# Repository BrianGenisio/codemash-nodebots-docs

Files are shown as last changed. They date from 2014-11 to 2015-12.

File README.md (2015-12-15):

# Website for [NodeBots.CodeMash.org](http://nodebots.codemash.org)

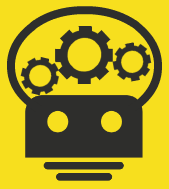
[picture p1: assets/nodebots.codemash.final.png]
NodeBots CodeMash logo


This site uses [Jekyll](http://jekyllrb.com/) and GitHub Pages to host.  **Pull Requests are accepted!**  If it is just a small Markdown change, you can go into the "_posts" folder right from GitHub to edit and create an automatic fork/PR without cloning the repo onto your machine.  If you want to do more, install Jekyll, clone the repo, and run `jekyll serve --watch` from the "gh-pages" branch.

**Note**: This is the site for Nodebots @Codemash 2015.  For the 2016 event, please see [the NodeBots Unleashed site.](https://github.com/CareEvolution/nodebots-unleashed-codemash-docs)

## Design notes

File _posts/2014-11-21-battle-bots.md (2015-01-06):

---
layout: page
title: "Battle Bots"
category: act
date: 2014-11-21
order: 0
---

One of the activities at this event is "Battle Bots".  When you build a battle bot, you are competing in a head-to-head battle, much like a wrestling or sumo match.  There will be a ring, and your job will be to push your opponent out of the ring.

**Here are the rules**

0. Build your bot however you want, but use the two continuous servos as your primary drive mechanism.
0. The arena is a hexagon, 1 meter wide, on carpet.
0. You have one minute to knock your opponent completely out of the arena.  This is considered a KO.
0. If after one minute, a KO is not achieved, the bot with their Arduino closest to the center dot wins.
0. We will set this up as a randomized single-elimination bracket, so build your bot to fight more than once.
0. All rules are subject to interpetation by the referee.

You have full access to the maker space.  If you build the reference kit, you are very unlikely to win.  You need to innovate.  What kinds of modifications can you make to give yourself an advantage?

**Here are some examples of NodeBots battling it out**

<iframe width="640" height="360" src="//www.youtube.com/embed/pmp_hCg6jGQ" frameborder="0" allowfullscreen></iframe>

**And here is an example of an intense battle**

<iframe width="640" height="360" src="//www.youtube.com/embed/OA97THHGgEo" frameborder="0" allowfullscreen></iframe>

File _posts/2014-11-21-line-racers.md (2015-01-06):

---
layout: page
title: "Line Racers"
category: act
date: 2014-11-21
order: 1
---

If you are feeling more like a pacifist and you don't want to fight your bot, then perhaps you would like to race your bot?  Your line racer will follow a dark line on a white background and will traverse the path as quickly as possible.  You will be given a "reflectance sensor kit" which can be used to detect your position on the line.  

**Here are the rules:**

0. You may use any materials you wish to build your bot.
0. You will be timed as you traverse the track once without user intervention.
0. A 6" perpendicular line will indicate the start/finish line (same spot).  Your sensor will start on this line and your bot must stop on the line.  Failure to stop will result in a 6 second penalty.
0. Your line sensor must stay on the line at all times.  Failure to do so will result in a 2 second penalty for each divergence. The referee reserves the right to disqualify any both which flagrantly diverges from the course.
0. The minimum turn radius will be 2 inches.
0. There is at least 3 inches between the edge of the line and the edge of the platform or other line.
0. Bots which take more than 1 minute to complete will be disqualified.
0. All rules are subject to interpetation by the referee.

**Here is an example of a line-following bot**

<iframe width="640" height="360" src="//www.youtube.com/embed/i6n4CwqQer0" frameborder="0" allowfullscreen></iframe>

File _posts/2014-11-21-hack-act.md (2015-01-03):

---
layout: page
title: "Hacking"
class: hack-act
category: act
date: 2014-11-21
order: 2
---

Perhaps you don't want to compete with anyone.  That is totally fine!  You can just hack.  Come up with an idea, and go to town.  We have a fully-stocked lab with all sorts of chassis, building materials, controller boards, electronic components, and tools.  Checkout our inventory for more information about what we have for you to build with.  Build whatever you want.  Just make sure to "show and tell" at the end.  We can't wait to see what you build.

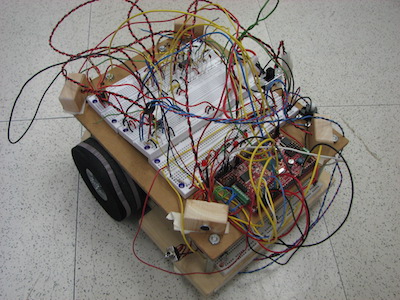
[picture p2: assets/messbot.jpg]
messy bot


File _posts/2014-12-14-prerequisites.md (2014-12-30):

---
layout: page
title: "Prerequisites"
category: tut
date: 2014-12-23
order: 0
---

0. [Node.js (required)](#nodejs)
0. [Arduino IDE (required for Windows)](#arduino)
0. [Git (optional but recommended)](#git)
0. [Visual Studio Tools (optional)](#vs)
0. [Sublime Text (optional)](#sublime)

> All of the files have been packaged up into a [single location](https://www.dropbox.com/sh/v4krjmg3rcctdvw/AADja4svpkxiA2zTXFDZe0PYa?dl=0) for your convenience.

## Node.js (required) 
This is the only required software.  These are [NodeBots](http://nodebots.io) so they require [Node.js](http://nodejs.org) to run. Node is a JavaScript runtime based on the V8 engine.  It is how you will be running the code today.  Just download and install it.

- [OSX](http://nodejs.org/dist/v0.10.35/node-v0.10.35.pkg)
- [Windows 32bit](http://nodejs.org/dist/v0.10.35/node-v0.10.35-x86.msi)
- [Windows 64bit](http://nodejs.org/dist/v0.10.35/x64/node-v0.10.35-x64.msi)

## Arduino IDE (required for Windows)
The Arduino IDE is useful if you want to run native C code with your Arduino boards.  In this lab, we will be using JavaScript on a host computer which communicates over serial to the Arduino.  We've pre-loaded the required code on your board, so you don't need the Arduino IDE for much.  It does, however, install some necessary drivers for USB to Serial in Windows.  You might want it, also, if you want to do more advanced things with your hardware.  After you install it, run it once.

- [OSX](http://arduino.cc/download.php?f=/arduino-1.0.6-macosx.zip)
- [Windows](http://arduino.cc/download.php?f=/arduino-1.0.6-windows.exe)

## Git (recommended)
The open source community runs on [Git](http://git-scm.com/) and [GitHub](http://github.com).  All of our examples as well as anything else you are likely to want to bring in will be on Git.  Because of this, we recommend that you have Git.  You can get away with not installing it if you prefer -- you can just download Zip files from GitHub -- so it is optional.  If you don't already have Git installed, we recommend installing the GitHub client on Windows.  For the Mac, open up a command line and type `git --version`.  If it is already installed, you will get a version back.  If not, OSX will ask you to install the necessary components automatically.

- [Windows](https://github-windows.s3.amazonaws.com/GitHubSetup.exe)

## Visual Studio Tools for Node.js (optional for Windows)
Some Windows users prefer the Visual Studio environment when developing in Node.  If you think you'd like to do that, you can install the tools for Visual Studio 2012 or 2013

- [VS 2012](http://nodejstools.codeplex.com/downloads/get/946896)
- [VS 2013](http://nodejstools.codeplex.com/downloads/get/946895)

## Sublime Text (optional)
You need a text editor.  Chances are that you already have one that you like.  If not, try Sublime Text.  It is pretty nice.

- [OSX](http://c758482.r82.cf2.rackcdn.com/Sublime%20Text%202.0.2.dmg)
- [Windows 32bit](http://c758482.r82.cf2.rackcdn.com/Sublime%20Text%202.0.2%20Setup.exe)
- [Windows 64bit](http://c758482.r82.cf2.rackcdn.com/Sublime%20Text%202.0.2%20x64%20Setup.exe)

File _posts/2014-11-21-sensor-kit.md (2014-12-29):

---
layout: page
title: "Adding Line-Following Sensors"
category: tut
date: 2014-11-21
order: 4
---

## What you need

To build a line-following bot, you will need to add a sensor array to the reference kit. To do so, you will need:

 - (1) [Reference kit bot](http://nodebots.codemash.org/tut/building-the-reference-bot.html)
 - (1) IR Reflectance Sensor Array
 - (1) Female-to-female ribbon cable with at least 9 wires
 - Padded double-sided tape
 
As with the reference kit, you are encouraged to pursue your own design when adding line-following to your bot. However, this is an example of how you can simply extend a bot to make it a line-follower.

## Orient the sensor array
Before attaching the sensor, make sure it is oriented correctly. The pins should be pointing up toward the chassis and the sensors (small black rectangles) down toward the ground. In addition, considering that the front of the bot is where the wheels and servos reside, pin 1 should be toward the left wheel, pin 6 toward the right.

## Attach the sensor array to your chassis

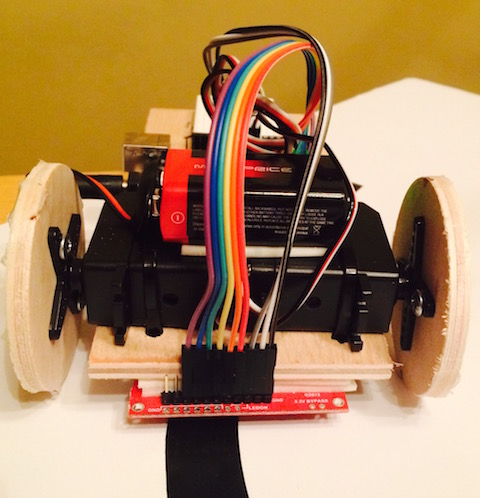
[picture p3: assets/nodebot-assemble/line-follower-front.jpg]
Line follower front view


As shown in the preceding image, use strips of padded double-sided tape to mount the sensor array between the wheels at the front of the bot. Ensure that the array sits within one quarter of an inch of the line to be followed by doubling up the padded tape as needed (or using some other padding material).

## Connect the sensor array to the Ardiuno

Using the ribbon cable, connect the sensor array to the Arduino board according to the following wiring diagram (the wire coloring matches that of the provided photos).

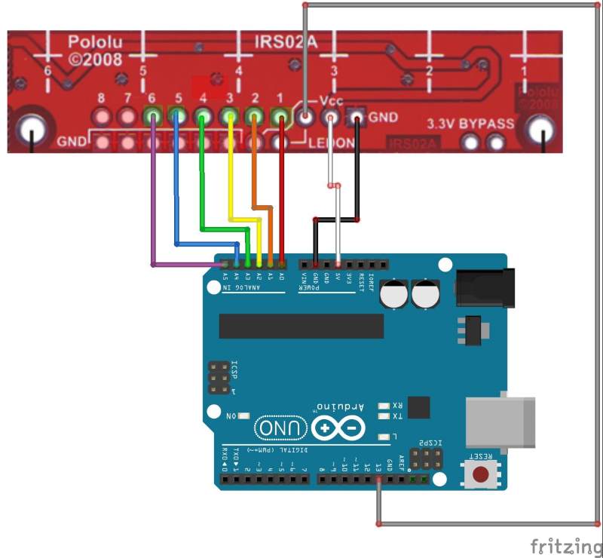
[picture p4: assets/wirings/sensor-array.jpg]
Line follower wiring


The following image shows the Arduino end of the connections.
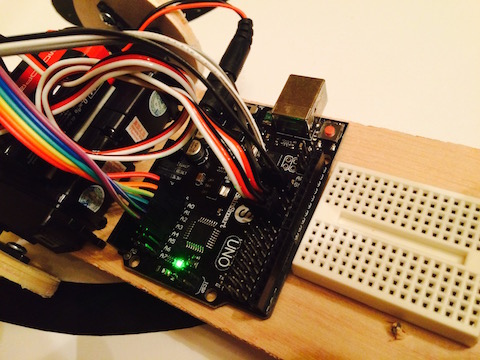
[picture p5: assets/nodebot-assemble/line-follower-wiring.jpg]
Line follower wiring view


## Reprogram your bot

Now that the hardware is ready, you need to program your bot to follow a line. The following code provides a useful starting point for your line-following bot.

**bot.js**

<script src="http://gist-it.appspot.com/github/BrianGenisio/codemash-nodebots-docs/blob/master/examples/base-line-follower.js"></script>

**__NOTE:__** When you run this code (`node bot.js`), the wheels may start spinning.  They have been centered, so this means they need to be trimmed until they stop spinning.  Use a screwdriver and trim them until they are silent.

### Resources:
- [Johnny-Five Docs](https://github.com/rwaldron/johnny-five/wiki/Servo)
- [Johnny-Five Servo Docs](https://github.com/rwaldron/johnny-five/wiki/Servo)
- [Johnny-Five IR Reflectance Array Docs](https://github.com/rwaldron/johnny-five/wiki/IR.Reflect.Array)
- [Reading Keypresses](http://stackoverflow.com/questions/5006821/nodejs-how-to-read-keystrokes-from-stdin)

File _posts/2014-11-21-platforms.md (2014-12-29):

---
layout: page
title: "Platforms"
category: ref
date: 2014-11-21
order: 3
---

We have several "experimental" platforms that you can play with.  You may wish to use these instead of the supplied wood.  They are first-come, first-serve.

## Omnibot
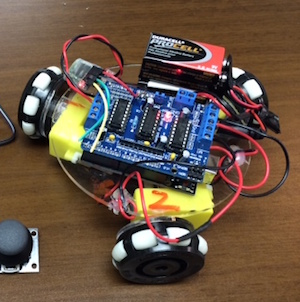
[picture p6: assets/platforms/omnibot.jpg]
omnibot


The Omnibot is cool because it can move in any direction at any time with its three omni-dirctional wheels.  You'll need a motor controller and have to figure out the vector math to make it work, but the possibilities are pretty cool.  We have three of these to hack with.

## Magician's Chassis
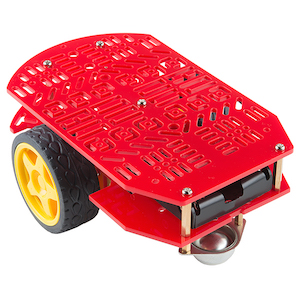
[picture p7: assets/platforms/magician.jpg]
Magicians Chassis


The Magician's Chassis is a beefed up version of the basic kit we are supplying you with.  The key differences is that it has more ways to mount things and it runs off of gearmotors instead of servos (though you can probably hook servos up instead).  You'll need a motor controller to power this thing, but they are EASY to use.  We have three of these to hack with.

## Tank
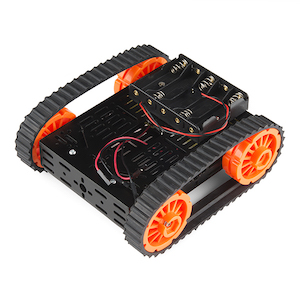
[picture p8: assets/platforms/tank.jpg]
Tank


We have a tank!  It is made of metal and has tank treads.  Pretty cool!  It runs off of motors, so you will need a motor controller of some sort.

## Gearboxes and Wheels
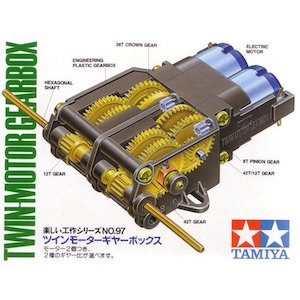
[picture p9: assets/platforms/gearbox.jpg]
Gear box


We have a couple of configurable gearboxes for extra power.  They come with some basic wheels.  You will need a motor controller to drive these motors.

## Sumobot Jr
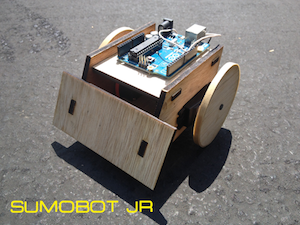
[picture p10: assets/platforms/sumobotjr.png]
Sumobot Jr


The Sumobot Jr is a neat little chassis.  It uses continuous servos and packs a lot into a small amount of space.  We have one of these.

## Dune Buggy Car
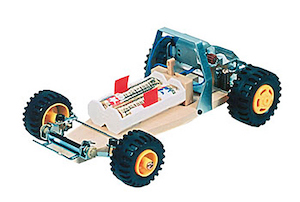
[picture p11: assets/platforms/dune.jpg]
Dune Buggy


The Dune Buggy Car will need some creative steering applied to it, but it is a spritely little chassis.  With two different gear ratios, this thing can go fast!  You will need a motor controller to drive this motor.

## Pan/Tilt Platform
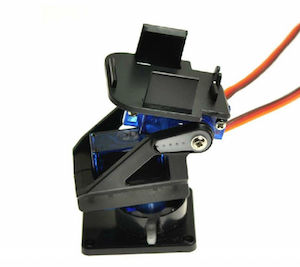
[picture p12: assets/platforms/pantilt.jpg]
Pan/Tilt Platform


We have a pan/tilt platform controlled by micro servos.  We aren't sure what you will do with this, but that's up to you!

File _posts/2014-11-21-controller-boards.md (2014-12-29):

---
layout: page
title: "Alternative Controller Boards"
category: ref
date: 2014-11-21
order: 4
---

If you'd like to experiment with something other than an Arduino, we have some alternative computers that you can use.  These units all have their own advantages over the Arduino but will take some extra tinkering to get them working.

## Electronic Imp
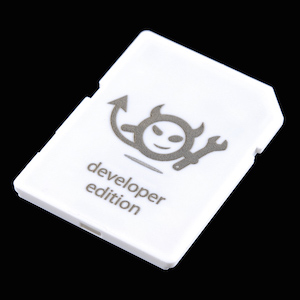
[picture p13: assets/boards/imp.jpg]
Electronic Imp


The [Electronic Imp](https://electricimp.com/) is a WiFi-enabled controller packed into a SD card.  It has a couple of GPIO pins and it fits into tight spaces.  You need to use the [Tyrion](https://github.com/rwaldron/tyrion) firmware with it and the [imp-io](https://github.com/rwaldron/imp-io/) adapter for Johnny-Five.

## Beaglebone Black
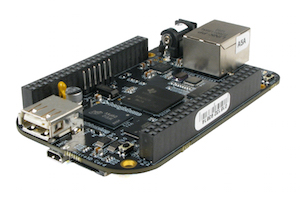
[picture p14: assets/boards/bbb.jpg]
Beaglebone Black


The [Beaglebone Black](http://beagleboard.org/BLACK) is a serious piece of equipment.  This thing comes with its own IDE!  Once you get it hooked up to WiFi (using the USB adapter), you can connect to it with your browser and program the board via the Cloud9 IDE. Johnny-Five is really easy to use with this board with the [Beaglebone-IO](https://github.com/julianduque/beaglebone-io) adapter.

## Spark Core
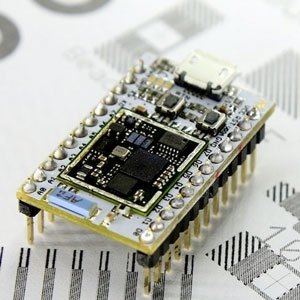
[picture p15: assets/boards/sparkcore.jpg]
Spark Core


The [Spark Core](http://docs.spark.io/) is a small chip with built-in WiFi and Arduino-compatible pin-outs.  It is easy to use with Johnny-five once you load the [Voodoospark firmware](https://github.com/voodootikigod/voodoospark#getting-started) and the [spark-io](https://github.com/rwaldron/spark-io/) adapter for Johnny-Five.

## Galileo
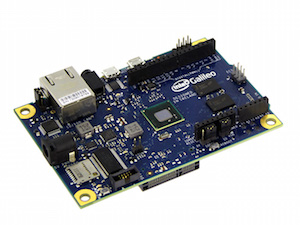
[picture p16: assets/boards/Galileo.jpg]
Galileo


The [Intel Galileo](http://www.intel.com/content/www/us/en/do-it-yourself/galileo-maker-quark-board.html) is a board with Arduino sockets but it runs Linux.  Actually, this particular board runs Windows 8!  But Johnny-Five won't run on Windows on this device.  You'll have to load the Linux image and then use the [Galileo-io](https://github.com/rwaldron/galileo-io/) adapter for Johnny-Five.

## Tessel
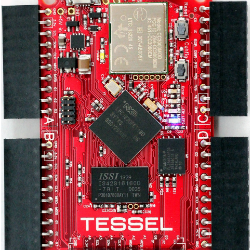
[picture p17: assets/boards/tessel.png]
Tessel


The [Tessel](https://tessel.io/) is interesting.  It is a WiFi enabled chip which runs JavaScript.  It is the only non-Linux based board in the flock that runs JavaScript natively.  Well, kind of.  It actually transpiles all of your JavaScript to Lua.  Unfortunately, this process is not compatible with the flavor of JavaScript that Node uses (V8).  Because of this, it doesn't run Johnny-Five.  It is still fun to play with.  It also includes a Bluetooth Low Energy add-on as well as a 12-servo add-on.  Perhaps you can do something cool with this?

## Extra Arduinos
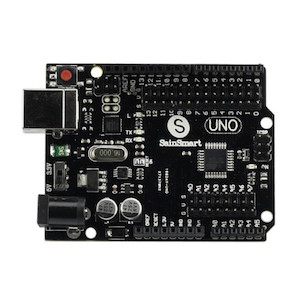
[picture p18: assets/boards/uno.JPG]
Sainsmart Uno R3


We also have several extra Arduino Unos for you to use.  Johnny-Five can support [multiple boards at the same time](https://github.com/rwaldron/johnny-five/wiki/Boards) so you aren't limited to a single board. You might also find a use for [remote-io](https://github.com/monteslu/remote-io) which allows you to remote-control Johnny-Five based devices.

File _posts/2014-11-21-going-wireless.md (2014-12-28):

---
layout: page
title: "Going Wireless"
category: ref
date: 2014-11-21
order: 2
---

Having your bot tethered to your computer via USB can be a real drag (lolz).  You may want to try going wireless.  We have some limited options for you.  They will take some tinkering with to get working, but they might be the advantage you are looking for.

## Bluetooth
We have about 6 JY-MCU Bluetooth to Serial adapters that can be used to make your bot wireless.  They take a bit of work to get going, and they can be finicky.  See the [JY MCU Bluetooth notes for Johnny-Five](https://github.com/rwaldron/johnny-five/wiki/JY-MCU-Bluetooth-Serial-Port-Module-Notes) for more information.

## Alternative Boards
Some of the alternative boards have built-in WiFi.  They include the SparkCore, The BeagleBone Black, The Electronic Imp, and The Tessel.  If you use one of those devices, you can achieve wireless control.  See the [Alternative Controller Boards]({{ site.baseurl }}/ref/controller-boards.html) for more information.

## WiFi
We have 5 ESP8266 WiFi to Serial adapters.  These crazy $4 units have their own GPIO pins and can be used standalone or connected to an arduino.  Only problem: we don't know how to use them.  There is an entire [community of hackers](http://www.esp8266.com/) who play with this chip.  Perhaps you will figure out something awesome to do with these?

## RF
We have two nRF24L01 RF modules that can be used to communicate.  We've never tried to get them working, so they will require some tinkering.

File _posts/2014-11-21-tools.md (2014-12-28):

---
layout: page
title: "Tools"
category: ref
date: 2014-11-21
order: 1
---

We have most of the tools that you are likely to need to build your ideas.For a full list of the components we have available to you, you can see our [Lab Inventory](https://docs.google.com/spreadsheets/d/1snX36J_Z5fDnIDeg48gQlfwQUidzGE4iUPnsUCTJoA8/edit#gid=1607775).  Some tools that are particularly interesting:

## Safety Goggles, Fire Extinguishers, and First Aid Kit
Saftety first, friends.  When working with soldering irons, drills, rotary tools, etc, please use safety goggles.  If we run into trouble, we have fire extuingishers and a first aid kit, but we'd really like it if we don't have to use them.

## Screwdrivers
We have lots of phillips and flathead screwdrivers of all sizes, though we don't have enough for everyone to keep for the entire time.  Please make sure to return them when you are done.

## Pliers and Wire Strippers
We have all the wire-cutting and stripping tools you need.  We also have a lot of pre-cut male/male, female/female and male/female wires.

## Scisors, Hacksaw, Exacto Knives
Need to cut things?  We have several pairs of scisors, exacto knives, a small hacksaw, and an acrylic cutting tool.

## Soldering Irons, and Support
We will have three soldering stations set up with solder, holders, solder removers, etc.  If you don't know how to solder, ask someone.  It is easy, but it is worth talking it through to make sure you don't burn yourself or damage the parts/equipment.

## Multimeters
We have three multimeters.  These tools are useful for measuring voltage, resistence, and current.  They are debuggers for electronics.

## Hot Glue Guns
Hot glue is one of the most versitile adhesives in a hacker's toolbox.  It hardens quickly, and most things stick together with it.  We have two glue guns hot and ready.

## Drill and Bits
We have a drill for you to use along with assorted driver bits and drilling bits.  **Please wear safety goggles!**

## Rotary Tool and Bits
Known by the more common brand name "Dremel", rotary tools are kind of like drills but are used to cut, grind, sand and buff.  We have an assortment of rotary tool bits for these applications.  **Please wear safety goggles!**

## Other Tools
Just because it isn't listed here, we might have a tool you need.  Just ask us!

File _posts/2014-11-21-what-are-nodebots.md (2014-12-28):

---
layout: page
class: what-is-nodebots
title: "What Are NodeBots?"
category: doc
date: 2014-11-21
order: 0
---

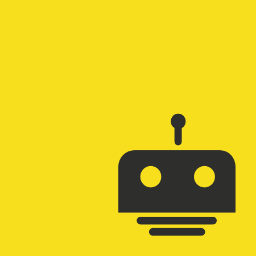
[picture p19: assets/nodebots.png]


[NodeBots](http://nodebots.io) are any kind of physical machine powerd by JavaScript and [Node.js](http://nodejs.org).  These "bots" can be drones, vehicles, sumos, humanoids, robot arms, connected thermostats, pretty LED arrays, weather stations, augmented clothing, or anything else you can imagine combining software with hardware and electronics.

Although this event will use Arduinos, the "brains" of a NodeBot can be any microcontroller that can run JavaScript or communicate to a controller running JavaScript.  These "brains" can include (but are not limited by) [Arduinos](http://arduino.cc), [Raspberry Pis](http://www.raspberrypi.org), [Spark Cores](https://www.spark.io/), [Electronic Imps](https://electricimp.com/), [Galileos](http://www.intel.com/content/www/us/en/do-it-yourself/galileo-maker-quark-board.html), [Edisons](http://www.intel.com/content/www/us/en/do-it-yourself/edison.html), and [BeagleBones](http://beagleboard.org/black).

We will be using [Johnny-Five](https://github.com/rwaldron/johnny-five), a JavaScript library for controlling your bot.  We like Johnny-Five because it is a very nice abstraction for the hardware, making the programming of these devices extremely accessible.  Some have called it "jQuery for hardware" because it tries to abstract the hardware details away from you and give you a standardized API for accessing devices like servos, motors, reflectance arrays, relays, shift registers, etc.

<div id="carousel-example-generic" class="carousel slide col-md-8 col-md-offset-2" data-ride="carousel">
  <!-- Indicators -->
  <ol class="carousel-indicators">
    <li data-target="#carousel-example-generic" data-slide-to="0" class="active"></li>
    <li data-target="#carousel-example-generic" data-slide-to="1"></li>
    <li data-target="#carousel-example-generic" data-slide-to="2"></li>
    <li data-target="#carousel-example-generic" data-slide-to="3"></li>
  </ol>

  <!-- Wrapper for slides -->
  <div class="carousel-inner" role="listbox">
    <div class="item active">
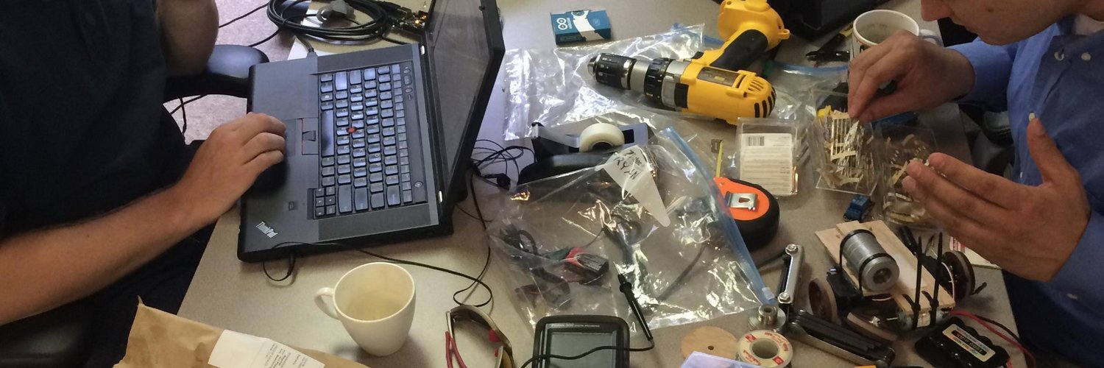
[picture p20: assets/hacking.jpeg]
      
    </div>
    <div class="item">
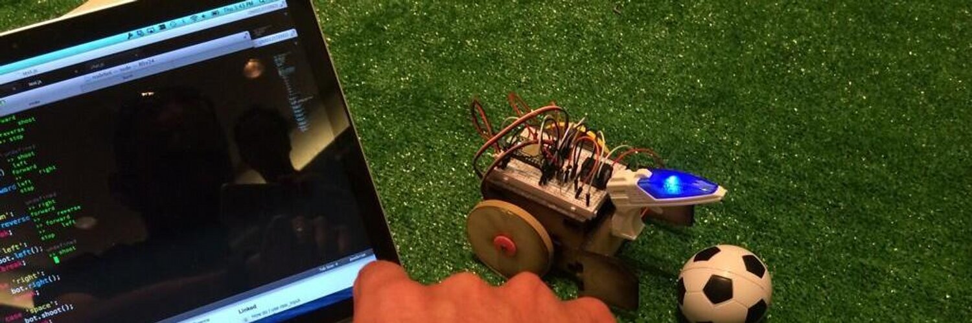
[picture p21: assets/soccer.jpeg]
      
    </div>
    <div class="item">
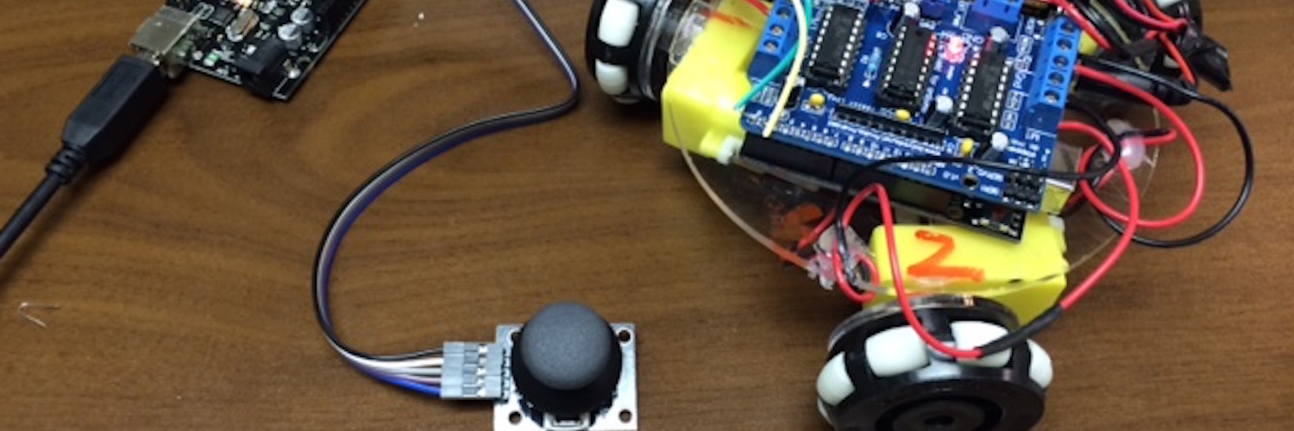
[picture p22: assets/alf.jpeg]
      
    </div>
    <div class="item">
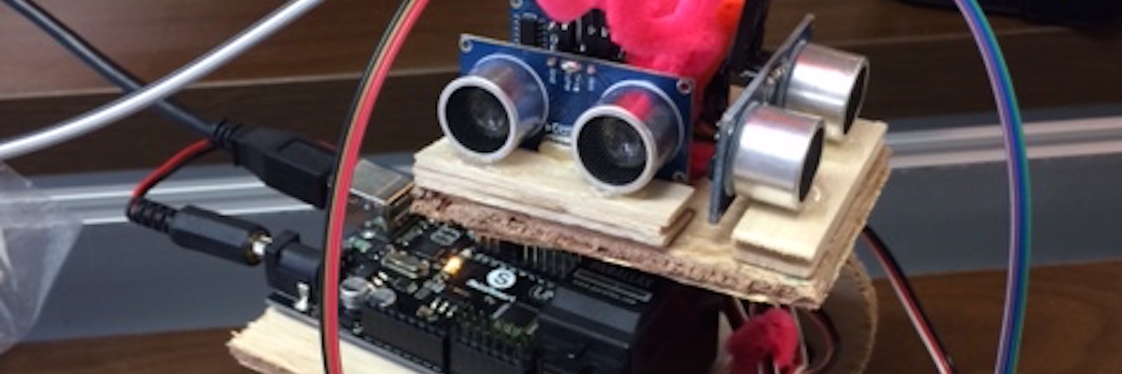
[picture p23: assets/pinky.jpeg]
      
    </div>
  </div>

  <!-- Controls -->
  <a class="left carousel-control" href="#carousel-example-generic" role="button" data-slide="prev">
    <span class="glyphicon glyphicon-chevron-left" aria-hidden="true"></span>
    <span class="sr-only">Previous</span>
  </a>
  <a class="right carousel-control" href="#carousel-example-generic" role="button" data-slide="next">
    <span class="glyphicon glyphicon-chevron-right" aria-hidden="true"></span>
    <span class="sr-only">Next</span>
  </a>
</div>

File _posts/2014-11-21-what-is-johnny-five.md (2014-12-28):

---
layout: page
class: what-is-johnny-five
title: "What Is Johnny-Five?"
category: doc
date: 2014-11-21
order: 1
---

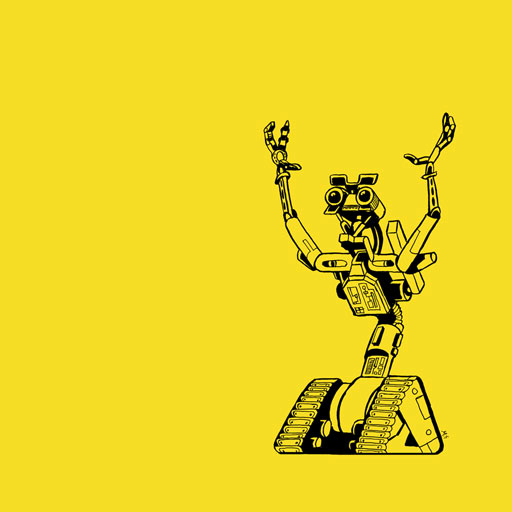
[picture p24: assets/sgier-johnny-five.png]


[Johnny-Five](https://github.com/rwaldron/johnny-five) is a [Node.js](http://nodejs.org) based robotics framework.  It has been compared to jQuery, but for hardware, because it normalizes hardware through a common API and has a similar event-driven interface.

There are several ways to run Johnny-Five, but in the case of the Arduino Uno boards in this lab, **the JavaScript does not run on the board**.  The JavaScript runs on your computer and communicates with the Arduino using [Firmata](http://www.firmata.org/wiki/Main_Page) which is a language-agnostic searial protocol for two-way IO communication.

You may wonder why we are using Johnny-Five and not running native C code on the device?  There is nothing stopping you from doing this, but we believe that Johnny-Five-based development is more interesting.

0. Running your code on a much more powerful controller system allows you to have access to more powerful capabilities.  Do you want to expose your hardware via an Express-based REST service?  You can do that by running your logic in Node.js.  You have access to everything in the NPM ecosystem.
0. Johnny-Five is an abstraction layer on top of what typical Arduino code looks like.  Instead of setting and reading values from pins, the Johnny-Five components create an interface for reading and writing that resembles what you are trying to achieve.  You don't need to translate your ideas to/from pin values.
0. This configuration prepares you for the next generation of systems.  Newer boards (Arduino Yun, Intel Galileo/Edison, Beaglebone Black, etc) will allow you to run JavaScript directly on the hardware.  Abstractions are the way to go!
0. Interacting with hardare is hard.  Using a language which more people are familiar with (JavaScript vs C) makes the hardware more accessible.
0. This is a great opportunity to learn Node.js if you don't already know it.  If you do already know it, your experience will feel very familiar.

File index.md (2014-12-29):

---
layout: index
title: "Welcome to NodeBots @CodeMash"
---



## Welcome to CodeMash NodeBots!

**[SAVE YOUR SEAT!  Supplies are limited!](http://www.codemash.org/save-seat2/)**

Armed with an Arduino, MacGyver-like circuitry, cheap wood, and JavaScript, can you rise to the call of battle? Engage your brain by building in three dimensions: software, electronics, and hardware. Innovate to give your bot the edge over your competition and battle for NodeBot supremacy. This precompiler is an all-day, hands-on, immersive experience. You don’t need to have any Node.js, hardware, or electronics experience — there will be coaches and pairs to work with you! Whose NodeBot will reign supreme?

Feeling more like a pacifist? Compete in our Line Racer challenge instead. Don’t feel like competing? We’ll have all sorts of platforms, boards, components, supplies, etc for hacking robots however you want.

For more photos and musings, follow us on twitter! <a href="http://twitter.com/nodebots_cm"><i class="fa fa-twitter-square fa-2x"></i> @nodebots_cm</a>

We also have a Chat Room!

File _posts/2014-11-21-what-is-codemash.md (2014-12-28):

---
layout: page
class: what-is-codemash
title: "What is CodeMash?"
category: doc
date: 2014-11-21
order: 0
---

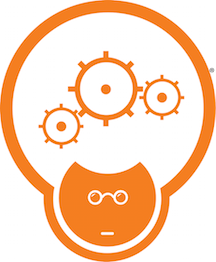
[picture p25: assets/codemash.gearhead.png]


[CodeMash](http://codemash.org) is a really great regional software conference in the Midwest.  CodeMash is home to some of the greatest technical polyglot content in the country.  Sporting over 2000 attendees, and hosted at an [indoor waterpark](http://www.kalahariresorts.com/ohio) in the dead of the winter, CodeMash has become a favorite technical conference for us all.

The conference, held over four days in January, is broken up into two "pre-compiler" days and two regular session days.  The "pre-compilers" feature half-day and full-day hands-on sessions.  This is when the NodeBots event will be held -- both days with different sets of hackers each day.

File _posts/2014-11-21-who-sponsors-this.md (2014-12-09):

---
layout: page
class: who-sponsors-this
title: "Who Sponsors This?"
category: doc
date: 2014-11-21
order: 2
---

CodeMash logo

[CareEvolution](http://letsfixhealthcare.com/) is a healthcare IT company who is trying to fix healthcare as we know it.  What do tiny JavaScript-powered robots have to do with healthcare?  It is all about culture.  We believe that hacking is an important part of exploring new ideas and concepts.  Every 8 weeks, we hold a "hackathon" where we encourage our employees to try something new.  Sometimes, we introduce a new visualization into our product line.  Other times, we evalutate a new technology.  

Programming robots?  Sure!  Designing robots requires you to think, design, and debug in multiple dimensions.  By tackling problems in software, electronics, and the physical world, you are forcing yourself to think differently than you do every day.  That exercise relaxes your brain so that when it comes time to solve problems in your day job, you are more creative and more likely to think about problems from a different perspective.

If a culture like this sounds interesting to you, we encourage you to talk to us and help us: [LetsFixHealthcare.com](http://letsfixhealthcare.com/).

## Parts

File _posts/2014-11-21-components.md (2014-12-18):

---
layout: page
title: "Components"
category: ref
date: 2014-11-21
order: 0
---

We have a LOT of components to help you make your design a reality.  For a full list of the components we have available to you, you can see our [Lab Inventory](https://docs.google.com/spreadsheets/d/1snX36J_Z5fDnIDeg48gQlfwQUidzGE4iUPnsUCTJoA8/edit#gid=0).  Most of these components have a nice Johnny-Five abstraction.  Some components that are particularly interesting:

## Servos
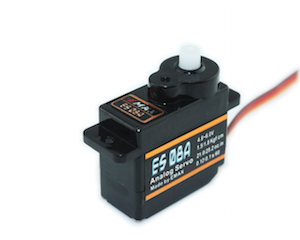
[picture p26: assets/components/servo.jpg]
Servos


Servos are a specific kind of motor which includes gearing and motor control built into the package. The servos you received in your kit are "continuous rotation" servos.  This means that they can rotate clockwise (`servo.cw()`) and counterclockwise (`servo.ccw()`) indefinately.  They work well for rotating the wheels of your bot.  You also have access to some standard servos which rotate (`servo.to(degs)`) to a specific value.  We have several standard-sized servos as well as several micro-sized servos.  [Johnny-Five Servo Reference](https://github.com/rwaldron/johnny-five/wiki/Servo)

## Motors, Gears, Wheels, HBridges, Motor Shields
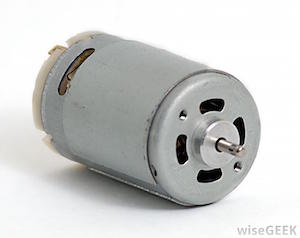
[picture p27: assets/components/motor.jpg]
Motor

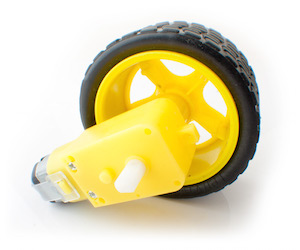
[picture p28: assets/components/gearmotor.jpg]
Gearmotor

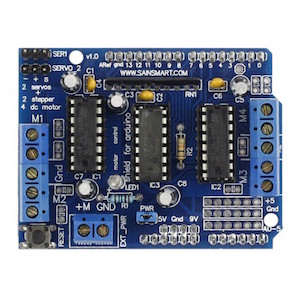
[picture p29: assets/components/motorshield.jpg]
Motor Shield


There are times when you want access to a vanilla motor.  These motors are much more simple than servos -- they don't have any gears or motor control circuitry -- so they give you more control.  We have gearboxes and wheels in order to transfer the motor's drive to much higher torque.  We also have HBridges which can drive a motor and control the direction.  We also have "motor shields" which plug into your Arduino and include the circuitry necessary to drive motors. [Johnny-Five Motor Reference](https://github.com/rwaldron/johnny-five/wiki/Motor)

## LEDs, Digit Displays, Matrix, Drivers
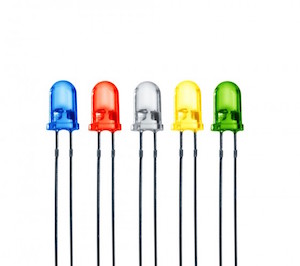
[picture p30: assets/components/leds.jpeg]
LED

LED RGB
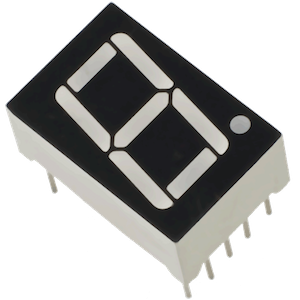
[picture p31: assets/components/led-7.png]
7-Segment LED

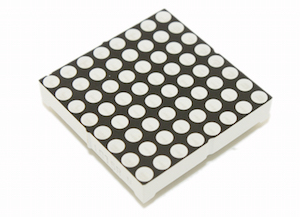
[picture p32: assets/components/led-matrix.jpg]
LED Matrix


Want to give visual feedback to the user?  We have hundreds of LEDs (Red, Gree, and Blue) as well as RGB units where you can set arbitrary colors.  We also have 7-segment displays.  These come in single-digit and 4x-digit packages.  You need a "driver" chip to decode these displays, which we have in the lab.  We also have several 8x8 LED arrays where you can create whatever pattern you want.  They take the same "driver" chip as the 7-segment components. [Johnny-Five LED Reference](https://github.com/rwaldron/johnny-five/wiki/Led), [Johnny-Five LED RGB Reference](https://github.com/rwaldron/johnny-five/wiki/Led-RGB), [Johnny-Five LED Digits Reference](https://github.com/rwaldron/johnny-five/wiki/Led.Digits), [Johnny-Five LED Matrix Reference](https://github.com/rwaldron/johnny-five/wiki/Led.Matrix)

## Joysticks
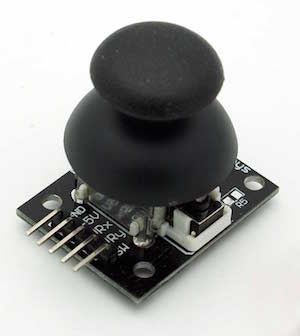
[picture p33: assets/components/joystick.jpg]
Joystick


We have a handful of Joystic controls that you can hook up for control.  They include X and Y directions as well as single push-buttons.  [Johnny-Five Joystick Example](https://github.com/rwaldron/johnny-five/blob/master/eg/joystick.js)

## Toggles, Pushbuttons, Relays
Toggle Switch
Momentary Switch
Relay

If you need switch inputs, you want to use a toggle switch or a push-button (momentary) switch.  If you'd like to control a switch, you want a relay.  [Johnny-Five Toggle Switch Example](https://github.com/rwaldron/johnny-five/blob/master/eg/toggle-switch.js), [Johnny-Five Button Reference](https://github.com/rwaldron/johnny-five/wiki/Button), [Johnny-Five Relay Reference](https://github.com/rwaldron/johnny-five/wiki/Relay)

## Buzzers
Piezo

If you want your bot to make a noize, you want a buzzer,  There are Active Piezos which make a sound when a voltage is applied.  There are also Passive Piezos which make a sound when a voltage is toggled.  Passive buzzers are good when you want to control the pitch.  You can even play songs with these buzzers! [Johnny-Five Piezo Reference](https://github.com/rwaldron/johnny-five/wiki/Piezo), [J5-Songs Reference](https://www.npmjs.com/package/j5-songs)

## Photosensors, Motion Sensors, Flame Sensors, Reflectance Sensors
Photosensor
Motion Sensor
Flame Sensor
Reflectance Array

We have all sorts of light-based sensors for you to work with.  Light sensors will detect ambient light.  They can also be controlled via laser pointers!  Motion sensors will detect when something is in front of it.  Flame sensors will detect flames!  Reflectance sensors will detect white vs black material.  They are great for writing line-following bots! [Johnny-Five Sensor Reference](https://github.com/rwaldron/johnny-five/wiki/Sensor), [Johnny-Five Reflectance Array Reference](https://github.com/rwaldron/johnny-five/wiki/IR.Reflect.Array)

## Ping (distance) Sensors
Ping Sensor

Ping sensors can tell you how far away an object is.  They send out an ultrsonic pulse and measure the time it takes to receive the response.  [Johnny-Five Ping Reference](https://github.com/rwaldron/johnny-five/wiki/Ping)

## Temperature, Humidity, Barrometric Pressure, Water Sensors
Temperature Sensor
Water Sensor

We have a handful of sensors that you can use to read the conditions around you.  Temperature sensors have a Johnny-Five abstraction but the others just need to use the Sensor class. [Johnny-Five Temperature Reference](https://github.com/rwaldron/johnny-five/wiki/Sensor), [Johnny-Five Sensor Reference](https://github.com/rwaldron/johnny-five/wiki/Sensor)

## Accelerometers and Gyros
IMU

Accelrometers are units that can tell you the XYZ orientation of an object.  Gyros can tell you the XYZ rotation of an object.  When used together, these units can tell you a lot about the inertial movement of your bot.  We have individual sensors, but we also have several units which have both sensors in one unit. [Johnny-Five Accelerometer Example](https://github.com/rwaldron/johnny-five/blob/master/docs/accelerometer.md), [Johnny-Five Gyro Reference](https://github.com/rwaldron/johnny-five/wiki/Gyro), [Johnny-Five IMU Reference](https://github.com/rwaldron/johnny-five/wiki/Gyro)

## Resistors, Capacitors, Transistors, Diodes
resistor
capacitor
transistor
diode

Many of the above components are contained and you don't need extra circuitry to power them.  You may find, however, that you need to build your own circuits.  Our assored resistors, capacitors, transistors and diodes should help you build most simple circuits.

## Breadboards, Wires, and Pins
Breadboard
wires
pins

Your kit includes a small breadboard.  We have several extra, larger breadboards.  We also have breadboard shields as well as solder boards for you to use.

## Batteries and Charger
9v
AA
AA clip

Your kit includes a 9V battery, which is necessary to power your higher-power devices (servos, motors, etc).  Should you spend all the energy in your battery, we have some extra 9V batteries.  We also have several AA batteries and 4x clips (6V).  We also have some high-capacity rechargeable batteries in stock.

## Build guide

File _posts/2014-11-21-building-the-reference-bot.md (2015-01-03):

---
layout: page
title: "Building the Reference Kit"
category: tut
date: 2014-11-21
order: 3
---
The kit you were given includes the following components:

- (1) [SainSmart Uno Arduino Clone](http://www.sainsmart.com/sainsmart-uno-r3-atmega328-au-development-board-compatible-with-arduino-uno-r3.html)
- 5mm Wood Platform -- (1) 3" x 6.75" panel and (2) 2.5" wheels
- (2) [Continuous Rotation Servos](http://www.amazon.com/NEEWER%C2%AE-Spring-SM-S4306R-Interface-degree/dp/B00EDESABU#)
- (1) [5/8" Ball Caster](http://www.amazon.com/TruePower-Roller-Ball-Transfer-Bearings/dp/B009KAQVWC/ref=sr_1_4)
- (1) [Small Breadboard](http://www.amazon.com/SYB-170-Color-Board-Small-Bread/dp/B00ARUF2JM/ref=sr_1_2)
- (6) [Solderless Breadboard Wires](http://www.amazon.com/Wosang-Solderless-Flexible-Breadboard-Jumper/dp/B005TZJ0AM/ref=pd_bxgy_e_img_y)
- (2) [3-pin Headers](http://www.amazon.com/5pcs-Angle-Single-Header-Strip/dp/B0079SK5MO/ref=sr_1_4)
- (1) 10' USB Cable (A to B)
- (1) 9v Battery
- (1) 9v to 2.1mm Battery Clip
- (4) Zipties
- (6) #6x3/8" Self-Drilling Screws
- (1) LED
- (1) 220 Ohm Resitor

You are encouraged to build your bot however you want, but this is how you can build it without any modifications from the original design.

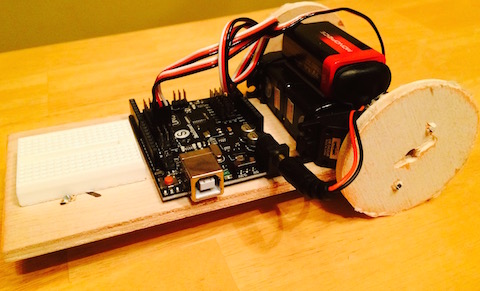
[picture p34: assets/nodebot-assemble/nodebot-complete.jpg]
Complete Bot


### Lay out your parts
You want to get a feel for where everything will go.  Lay your major components out on the board and rough-in where you think you'd like them to go.

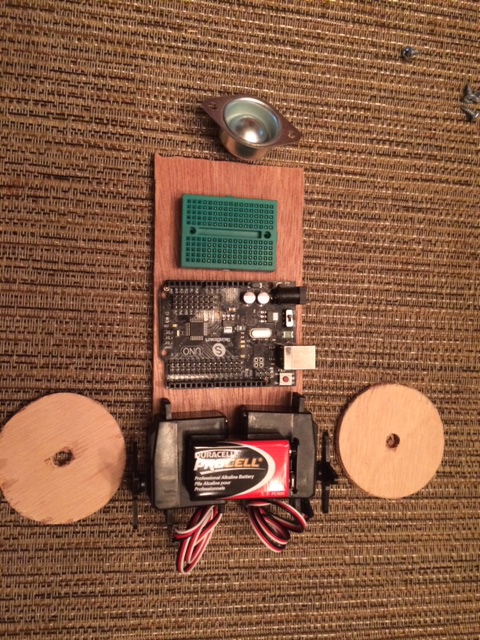
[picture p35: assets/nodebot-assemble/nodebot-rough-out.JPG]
Rough-out the parts


### Attach your wheels to your servos
Attach a servo horn (from those provided with the servo) to each of the wheels using the self-drilling screws.  The holes in the servo horn are smaller than the screws but these screws make quick work of the plastic and go right through to the wood (just make sure the servo horn is centered on your wheel). 

Once the horns are attached to the wheels, attach each wheel to a servo using the small black screws provided.

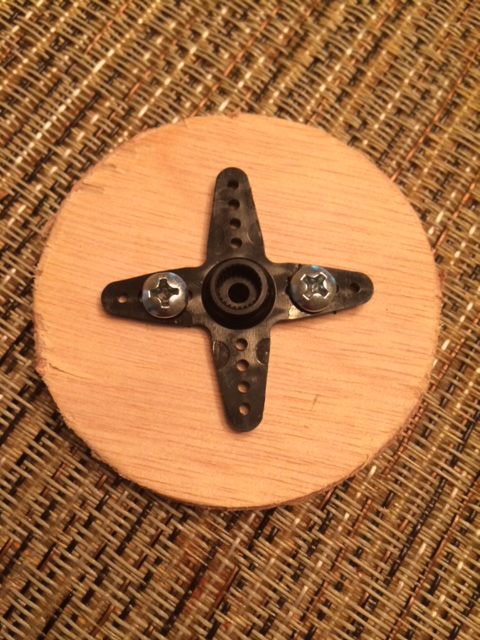
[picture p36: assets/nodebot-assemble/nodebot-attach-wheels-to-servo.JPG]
Attach the wheels to the servo horns


### Attach the servos to your chassis
Use two of the zip-ties to attach your servos to your chassis.  After they are tight, trim any excess.

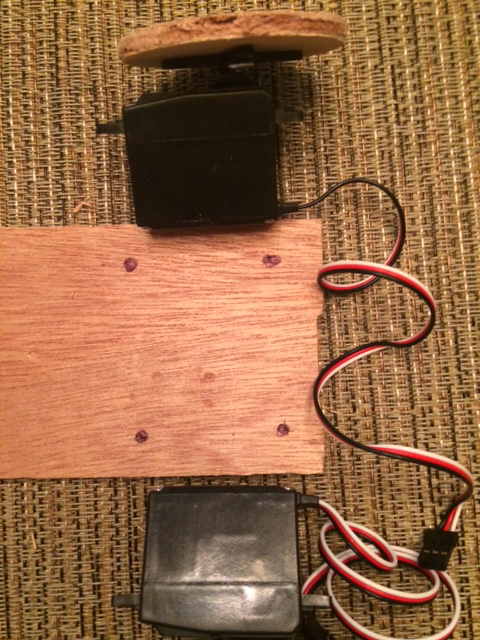
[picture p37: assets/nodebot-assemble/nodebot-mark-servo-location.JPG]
Mark your servo location

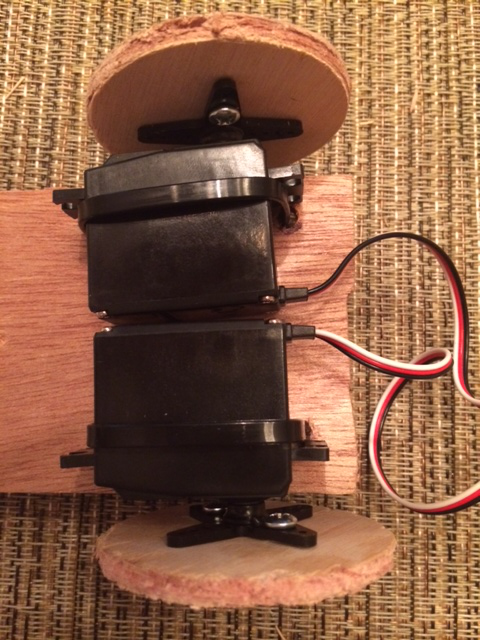
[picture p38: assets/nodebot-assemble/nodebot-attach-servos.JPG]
Attach the servos with zip-ties


### Attach the caster wheel to the bottom of the chassis
The self-drilling screws are really useful for this.

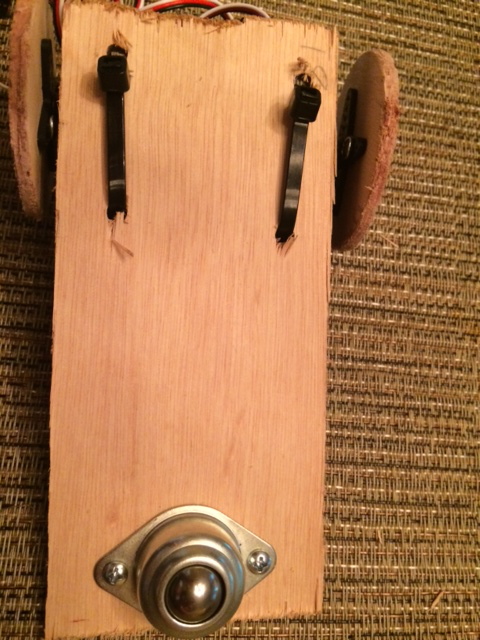
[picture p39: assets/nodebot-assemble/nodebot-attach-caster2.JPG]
Attach the front caster wheel


### Attach the Arduino and Breadboard
Affix the Arduino using double-stick tape.  Affix the breadboard using the attached mounting tape.

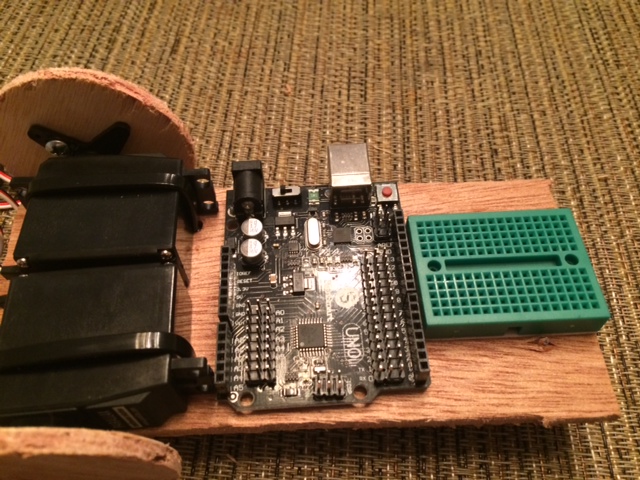
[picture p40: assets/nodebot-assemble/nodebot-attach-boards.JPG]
Affix the boards


### Mount the battery
Using double-stick tape, affix the battery to the bot.  Connect it to the Arduino using the 9v clip.  You may also find it useful to lay the battery on its side between the servos.

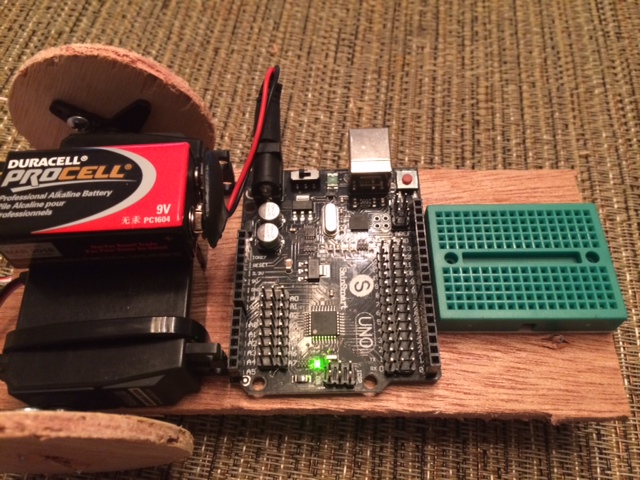
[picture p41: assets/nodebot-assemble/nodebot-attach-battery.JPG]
Affix the battery


### Power the servos from the board
You are not likely to keep the servos here permanently, but this is a good starting point.  Pins 9 and 10 support PWM signals, which are best for servos.  You can connect them to the SVG pin headers for now.  The white leads are the "signal" for the SVG pins.

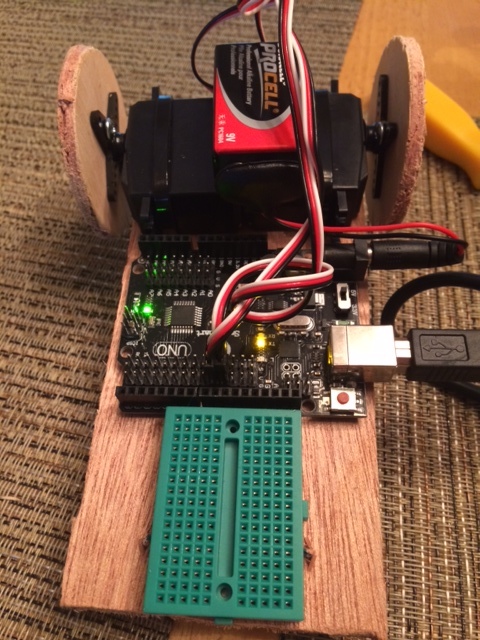
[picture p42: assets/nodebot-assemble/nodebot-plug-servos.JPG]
Power the servos


Your servos may start spinning now.  If that happens, you can trim them using the screws on the back of the servos.  You may need to do this again once you have hooked your system up to the software.

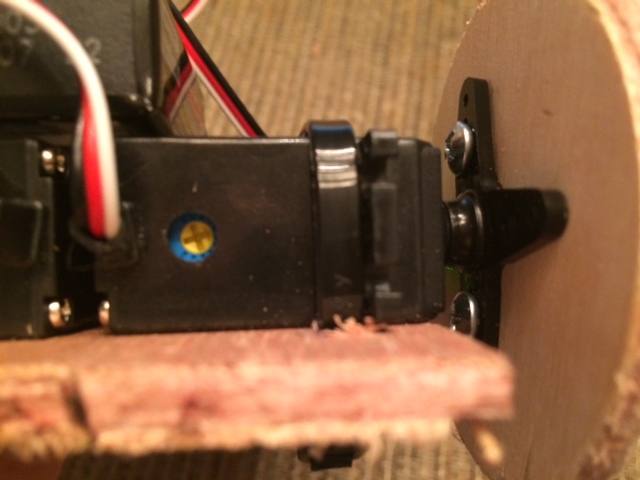
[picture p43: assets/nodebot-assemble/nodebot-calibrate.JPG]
Trim the servos


### Start programming your bot!

Now you have a working bot.  You can plug your USB cable into the board and get started.  Here is a good starting point:

**bot.js**

<script src="http://gist-it.appspot.com/github/BrianGenisio/codemash-nodebots-docs/blob/master/examples/base-sumobot.js"></script>

**__NOTE:__** When you run this code (`node bot.js`), the wheels may start spinning.  They have been centered, so this means they need to be trimmed until they stop spinning.  Use a screwdriver and trim them until they are silent.

### Resources:
- [Johnny-Five Docs](https://github.com/rwaldron/johnny-five/wiki/Servo)
- [Johnny-Five Servo Docs](https://github.com/rwaldron/johnny-five/wiki/Servo)
- [Reading Keypresses](http://stackoverflow.com/questions/5006821/nodejs-how-to-read-keystrokes-from-stdin)

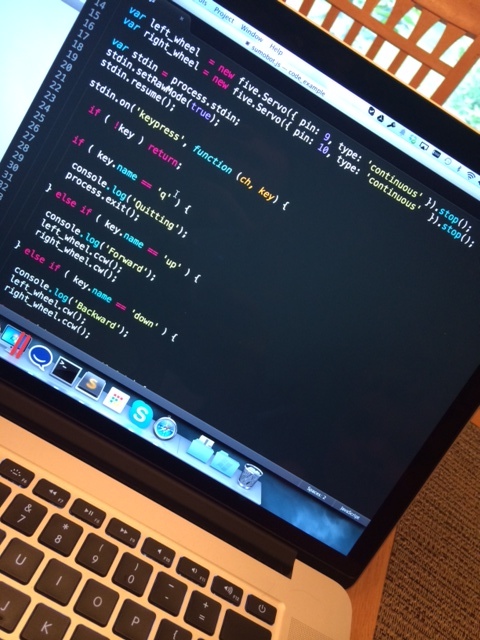
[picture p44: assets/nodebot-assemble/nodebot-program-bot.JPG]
Start Programming


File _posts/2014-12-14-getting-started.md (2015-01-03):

---
layout: page
title: "Getting Started"
class: getting-started
category: tut
date: 2014-12-23
order: 1
---

This guide is intended to get you familiar with using Johnny-Five to control inputs and outputs of your Arduino.  This section is completely optional, but it is a good way to start.  Do as much as you'd like, or jump right into building your bot.  Your choice!

WARNING: Some LEDs can be very bright, so you should avoid looking directly into them.

## Make an LED blink!
First step, let's make sure everything is working.  You will be running JavaScript on your computer which will communicate to your Arduino board via Serial.

In this example, we'll just get an LED to blink.

0. Make sure you've installed Node ([prerequisites]({{ site.baseurl }}/tut/prerequisites.html)) 
0. Connect your Arduino to your computer via USB
0. Open up a command prompt and create a folder to work in
0. From there, install Johnny-Five: `npm install johnny-five`.  This will install into your "node_modules" folder.
0. Create a file called "bot.js" and add the [LED Blink Code](#ledblink).
0. Wire up an LED (provided) to pin 11 with a resistor (provided) in serial to ground.
    - IMPORTANT: One leg of the LED is longer than the other. As shown in the wiring diagram below, make sure the shorter leg is connected to ground via the resistor and the longer leg is connected to pin 11.
0. Run your bot: `node bot.js`.  You should see the LED blinking!
    - If your LED is not lighting, double check you wired it correctly as noted in the previous step and shown in the wiring diagram below.

**LED Blink Code:**

<script src="http://gist-it.appspot.com/github/BrianGenisio/codemash-nodebots-docs/blob/master/examples/strobe.js"></script>

**LED Blink Wiring:**

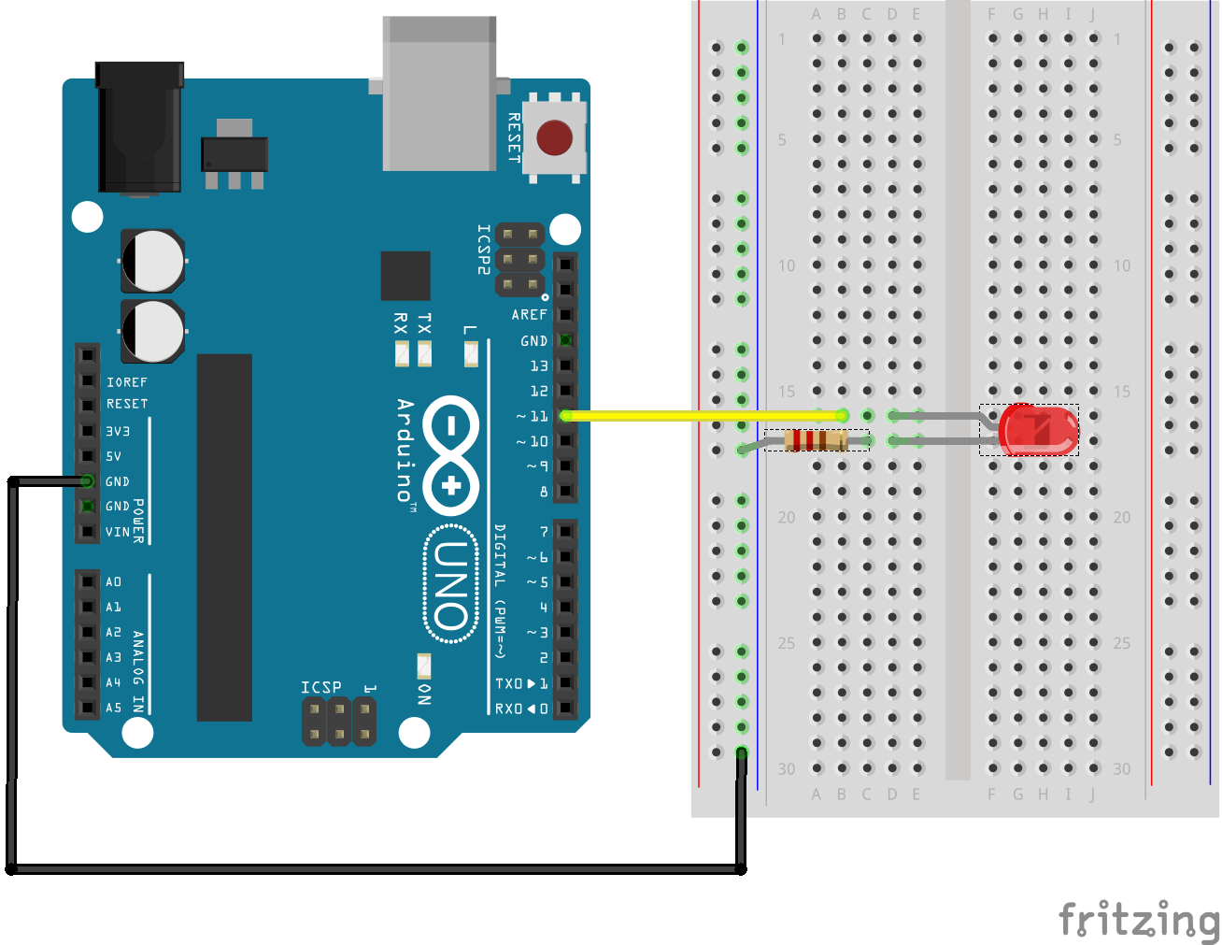
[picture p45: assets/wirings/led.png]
LED Wiring Diagram


## Make the LED pulse
In the last example, you told the LED to turn on and off.  Internally, the `strobe()` method just turns the pin high and low over time.  We'd like to change this program to fade in and out over time.  Instead of going high or low, you will be using the PWM (pulse width modulation) features of the board.  You can set the values to anywhere between `0` and `255` which will create a "square wave" with a duty cycle that simulates a "percentage on".  

Give it a try.  Change `strobe()` to `brightness(100)` and re-run your script.  Change the value from `100` to something else like `50` or `200`.  Notice how the LED brightness is controlled!

Now, change `brightness(100)` to `pulse(1000)`.  You are telling your LED to pulse between `0` and `255` over a 1-second interval.

## Read Input using a Potentiometer
A potentiometer (grab one from the lab) is a device that allows you to physically alter the resistance by turning a screw or sliding a lever.  It is a lot like a variable, but in hardware!  The included potentiometer is variable between 0ohm and 10Kohm over 20 full turns.  It has three pins.  The center pin will be variable and the outside pins will measure x or 10k-x.  

If you send a voltage from one outside pin to the ground of the other outside pin, the middle pin becomes a "voltage divider".  If you attach the center pin to an analog input on your Arduino, you can read the value (`0` through `1023`).

0. Put the potentiometer on your breadboard.
0. Connect the 5V line from your Arduino to one of the end pins of your potentiometer.
0. Connect the Ground line from your Arduino to the other end pin of your potentiometer
0. Connect the center pin of your potentiometer to the "Analog 0" (A0) pin on your Arduino.  [Wiring Diagram](#potinput_wiring)
0. Modify your "bot.js" file to include the [Potentiometer Input Code](#potinput) code.
0. Run your bot code and see the results on the screen.  Turn the potentiometer and see how the values change.  The changes are small.  Remember that this component is variable over 20 turns.

**Potentiometer Input Code:**

<script src="http://gist-it.appspot.com/github/BrianGenisio/codemash-nodebots-docs/blob/master/examples/read-sensor.js"></script>

**Potentiometer Input Wiring:**

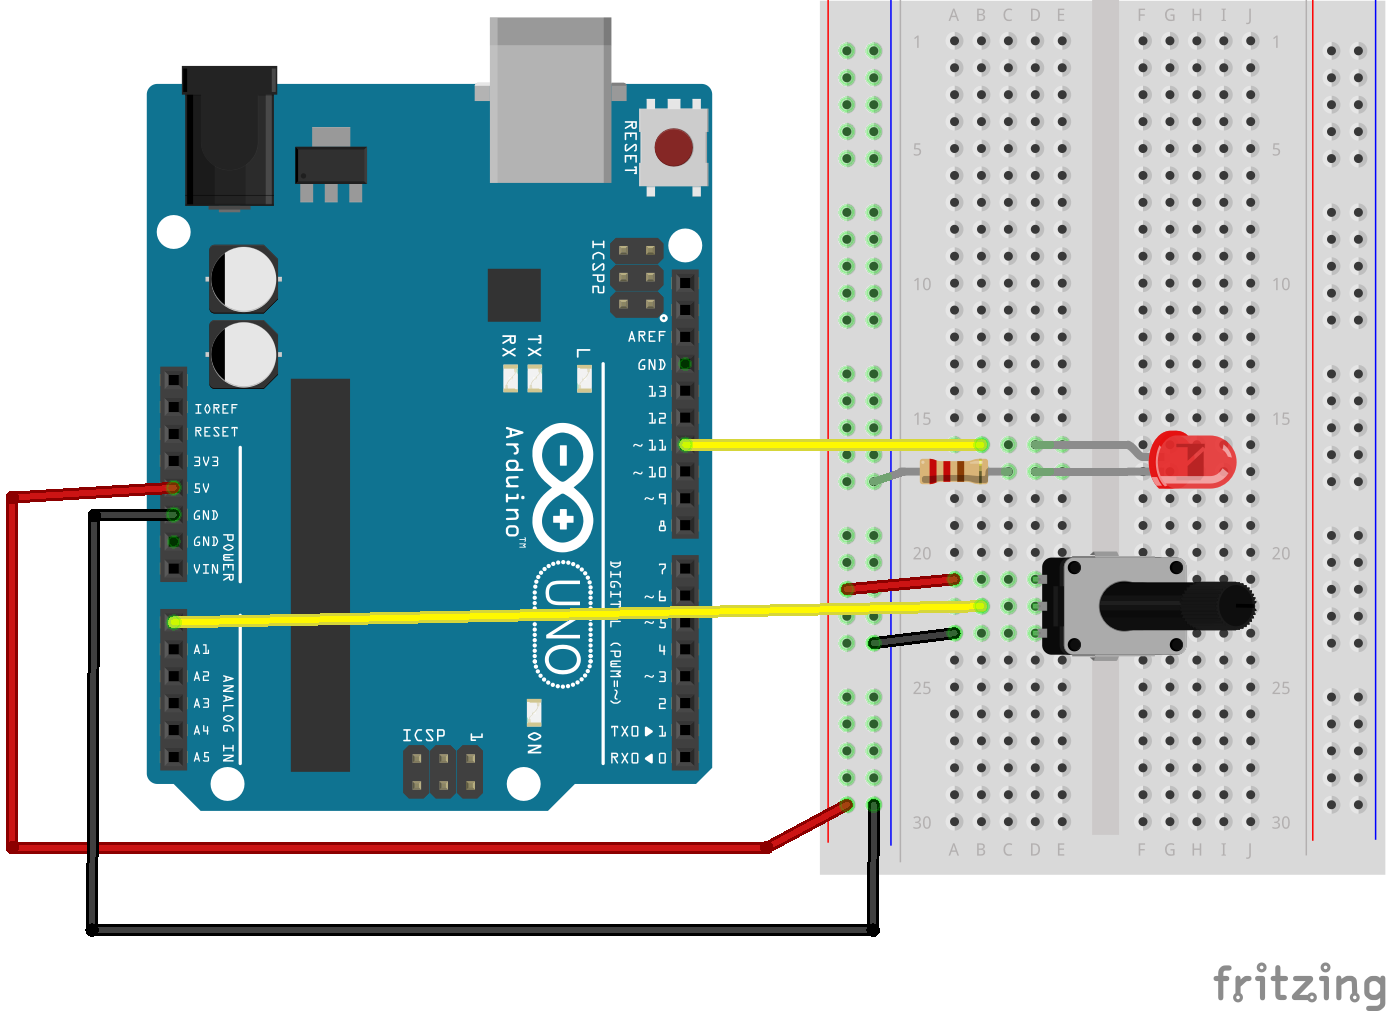
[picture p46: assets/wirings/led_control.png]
Potentiometer Wiring Diagram
 

## Control the LED using the Potentiometer
Now that you know how to control the brightness of your LED and you know how to read an input, let's put these two together.  You want small changes in your potentiometer to adjust your LED brightness, so you need to do some translation.  

Basically, you want to take the input value (between `0` and `1023`) and translate it to a value between `0` and `255`.  But you don't want to do a direct translation.  You'd have to change the potientometer a lot to see a little change.  

Instead, you can store the initial value and translate a swing of a small change to a percentage of the LED brightness.

0. Modify your "bot.js" code to include the [LED Control Code](#led_control)
0. Run your new code and see the brightness change by rotating the potentiometer.

**LED Control Code:**

<script src="http://gist-it.appspot.com/github/BrianGenisio/codemash-nodebots-docs/blob/master/examples/led_control.js"></script>

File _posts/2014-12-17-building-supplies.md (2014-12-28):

---
layout: page
title: "Building Supplies"
category: ref
date: 2014-11-21
order: 1
---

We have a lot of building supplies that you can use to build your ideas.  For a full list, see your [Lab Inventory](https://docs.google.com/spreadsheets/d/1snX36J_Z5fDnIDeg48gQlfwQUidzGE4iUPnsUCTJoA8/edit#gid=62263519).  Some tools that are particularly interesting:

## Wood
We have all sorts of wood to build with.  Much of it comes in small pieces of balsa, or dowel rods.  We also have extra wooden wheels and platforms.

## Foam Board
Foam board is great for prototyping.  It is relatively strong, and easy to cut.  We have foam board in all shapes and sizes.

## Acrylic Sheets
Also known as Plexi-Glass, acrylic sheets are very strong.  Consider cutting acrylic sheets with the "scoring tool" or the rotary tool.

## Glue, Tape, Staples, Velcro, Magnets, Zip Ties
We have lots of different kinds of adhesives.  Rubber cement, Elmers Glue, Crazy Glue, Single-sided tape, Double-sided tape, Electrical tape, Staples, Velcro, Magnets, Zip Ties (lots of them), and more. 

## Random Hardware
We have a lot of assorted random nuts, bolts, screws, etc.  

## Plasti Dip
Plasti-Dip is a paintable goo that dries as plastic.  It is useful for adding grip to any surface.  It does take a while to dry, but the heat gun helps accelerate that process.

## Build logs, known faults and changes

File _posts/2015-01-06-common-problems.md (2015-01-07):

---
layout: page
title: "Common Problems"
category: tut
date: 2015-01-06
order: 5
---

## Windows error when installing NPM:
> Error: ENOENT, stat `C:\Users\You\AppData\Roaming`

We're not sure why this happens, but it [sure is popular](http://stackoverflow.com/questions/25093276/node-js-windows-error-enoent-stat-c-users-rt-appdata-roaming-npm).  NPM can't find the folder that it is complaining about.  Create the folder, and it fixed the problem.

## You can't connect to the board in Windows
Sometimes, you need to specify your COM Port because it isn't automatically detected.  It is easy to [tell Johnny-Five which port to use](https://github.com/rwaldron/johnny-five/blob/master/docs/board-with-port.md).  

```js
board = new five.Board({
  port: "COM3"
});
```

You can open up the Arduino studio to see which port it finds.

## You get disconnected from the board when changing the rotation of your servo
This happens because your servos are drawing a lot of current through the board.  Your 9V battery is regulated down to 5V on the board, but when the current draw is too high, it can wreck havok on your board.

To solve this, you can power your servos directly from the battery instead of from the board.  You'll have to use more wires and your breadboard, but you will get a less noisy, more reliable system.

If you power your servos directly from a 9V battery, you are actually over-powering your components.  If you are willing to take the risk of buringing out your servos, then you will get a power boost.  If you'd rather not, you can get a 4xAA power source (6V) from the lab, or use a 5V regulator chip from the lab.

This is what your circuit will look like when the servos are directly connected:

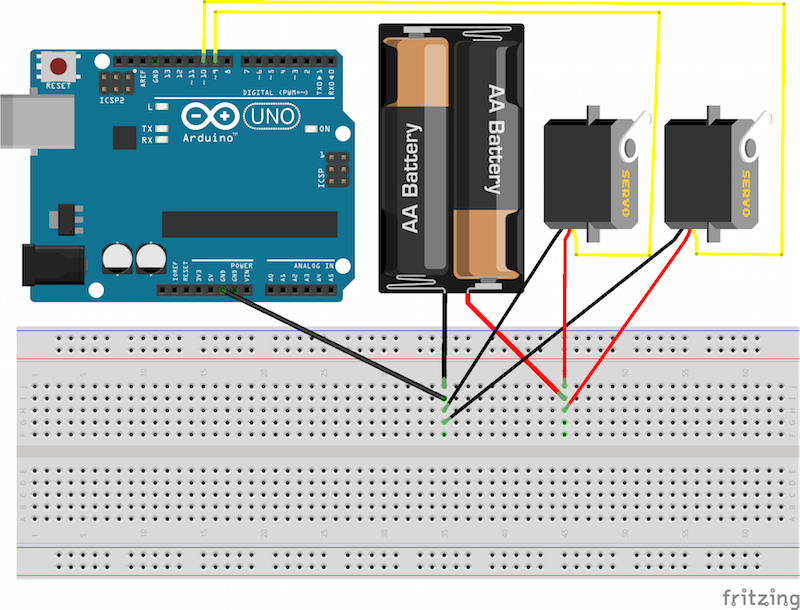
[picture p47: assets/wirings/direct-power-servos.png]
direct power wiring


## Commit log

2014-11-29 getting the landing page doing someting
2014-12-15 adding a getting-started guide
    [led.fzz, led_control.fzz]
2014-12-15 Update 2014-12-14-getting-started.md
    * Fixed various typos
    * changed five.Sensor("A0") to new five.Sensor("A0"), not because the other way didn't work, but because it's consistent with the other code doing new five.Board() and new five.Led(11). I think it's best to keep consistent instead of explaining to someone why they are different and why they both happen to work.
2014-12-20 Updated servo horn attachment
    See Trello:
    - https://trello.com/c/J61AePhP/69-website-instructions-for-reference-kit-don-t-specify-to-make-sure-wheels-are-screwed-to-the-servos
    - https://trello.com/c/zqiBP4Kb/68-website-servos-are-not-attached-to-the-horns-when-out-of-the-bag-so-description-to-detach-is-confusing
2014-12-20 Adding clarification on correctly wiring the LED
2014-12-20 Warning about LED brightness
    See trello:
    - https://trello.com/c/crl1pNDf/67-website-add-a-warning-to-help-prevent-looking-into-the-led-when-testing
2014-12-29 adding images for the special controller boards
2014-12-29 Adding fritzing diagram for reflectance sensor array
    [IRArray.fzz]
2014-12-29 Made wire colors match photograph
    [IRArray.fzz]
2014-12-29 Adding wiring image
2014-12-29 Resized wiring diagram
2014-12-29 Added servo trimming note & added resource links
2014-12-29 a couple of modifications
2015-01-07 adding a common problems page
    [Direct Power Servos.fzz]
